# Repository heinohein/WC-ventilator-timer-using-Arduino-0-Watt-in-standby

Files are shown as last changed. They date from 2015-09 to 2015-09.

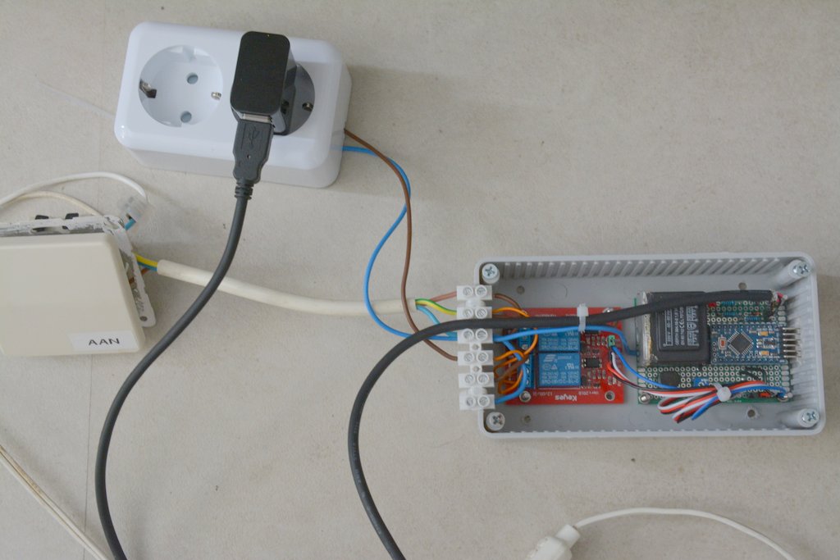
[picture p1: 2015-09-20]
WC-timer-pictures/WC timer 09 built together overview.JPG

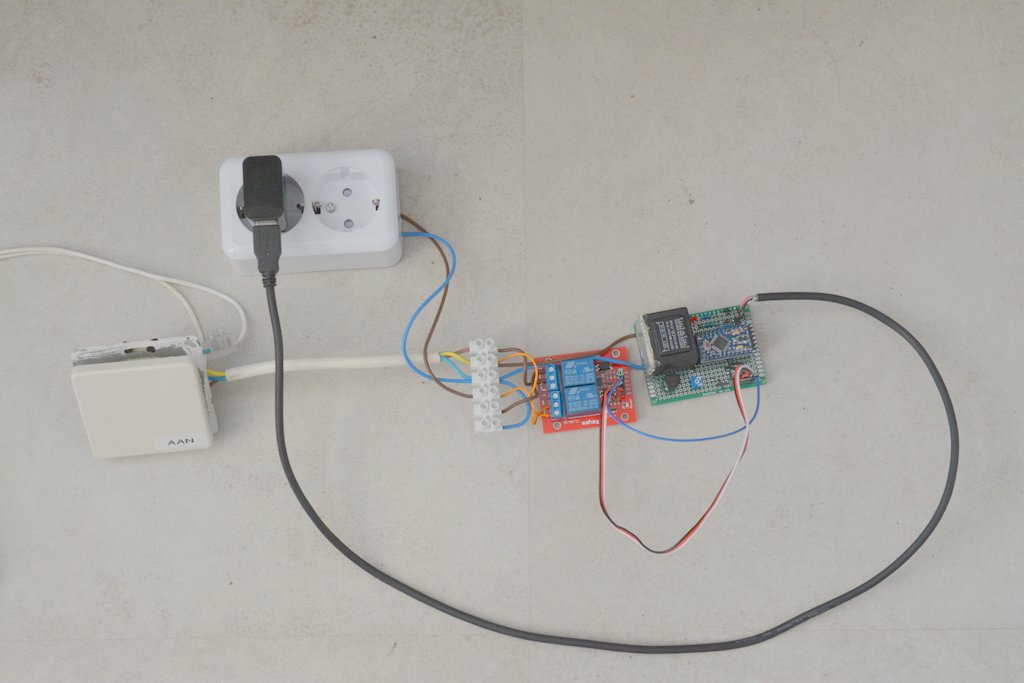
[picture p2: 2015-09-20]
WC-timer-pictures/WC timer 02 overview.JPG

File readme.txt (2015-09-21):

Timer for the motor of a WC ventilator using 0 Watt in standby

I wanted to create a timer for the ventilator in the WC, which consumes no electricity
when the timer is inactive. The project is based on using a Arduino Pro mini controling
a double relais "brick".

Priciple details:
The Arduino is fed by a 110-230V AC to 5V Dc transformer. This transformer is switched 
off AC by relais 1, hence 0 Watt standby. 
The motor of the WC ventilator is switched on/off by relais 2. 
When the lightswitch in the WC is switched on, it also provides power to Arduino. 
The Arduino detect by using a small 230V to 7,5 V transformer and some resistors 
(protected by a zener diode) that the lightswitch is switched off. This is the trigger 
that the timer can start counting down. 
The duration of the count down is variable adjustable by a potmeter.

PLEASE BE CAREFULL. 110-230V CAN KILL YOU!!.

Sketch details:
The map Arduino contains the sketch of the timer. All relevant variables are defined with
#define statements, and the sketch contains many comments for easy reading and amendment.
The sketch starts with a 10 seconds waiting. If the light in the WC is switched off during 
this time the motor of the ventilator will not run and the total electronic is switched off
again therefore using 0 Watt. If the motor of the ventilator is start running it will be 
minimal for 1 minute, independant of the input of the variable resistor. (to protect the 
motor).

Led of the Arduino:
off during initial 10 seconds wait
slow blinking during waiting for switching off 220V input (eg light WC)
faster blinking during count down and running of WC motor
very fast blinking after count down. This status is only visible if the 5V DC is not switched
off eg not the 0 Watt construction used.

PCB details:
The map Fritzing-schem-and-PCB contains a fritzing file. Inside this file you will find a
electric schem and the layout of a PCB. The schem and the PCB are also available as JPG 
in the map Wc-timer-pictures.

I designed a PCB based on a perfboard with copper solder rings on the bottom side. 
Only normal sized, not SMD components were used. 
I used for the actual build a two sided 5 x 7 cm perfboard, but did not use the toplayer 
solder rings. The few crossing wires on the topside are made of normal wires, as visible 
on the photo 05 and 06.

I could not find a propper footprint for the 230V to 7,5V AC transformer. So I used in the
schem a small audio transformer, and on the PCB I used via's to connect to the pins of the
actual transformer. This transformer feeds a led, so it is visible on the PCB that the light in
the WC is switched on.

The 230V to 5V DC transformer is switched on to power by plugging it in into a separate outlet.
Be aware that this outlet will only supply power when the WC light is switched on and the sketch
is running. See picture 02. 

The Arduino is connected to the PCB using 2x 12 pins female connector, eg the Arduino is removable.

Pictures:
Photo's of the final test setup before final installation can be found in map 
Wc-timer-pictures. 

Costs:
Total cost of the project ca. 20,45 eur/$. For details see file WC timer-bom2.html

Have fun.
HEINOHEIN

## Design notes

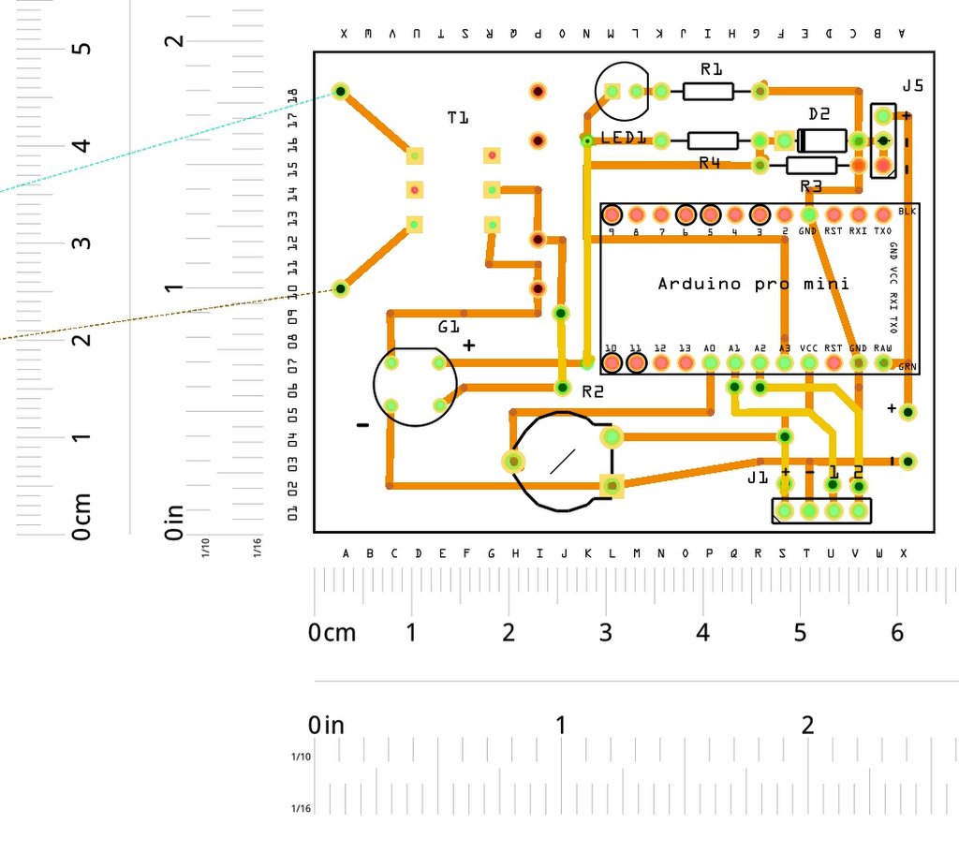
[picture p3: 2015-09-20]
WC-timer-pictures/WC timer_pcb overview.JPG

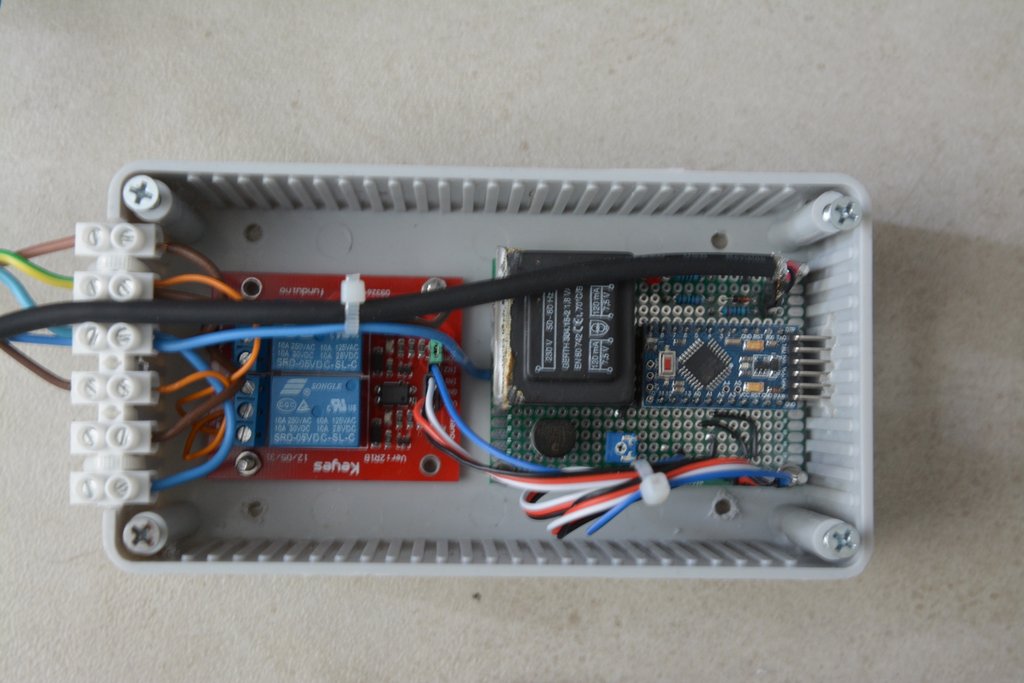
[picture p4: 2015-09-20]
WC-timer-pictures/WC timer 10 built together detail.JPG

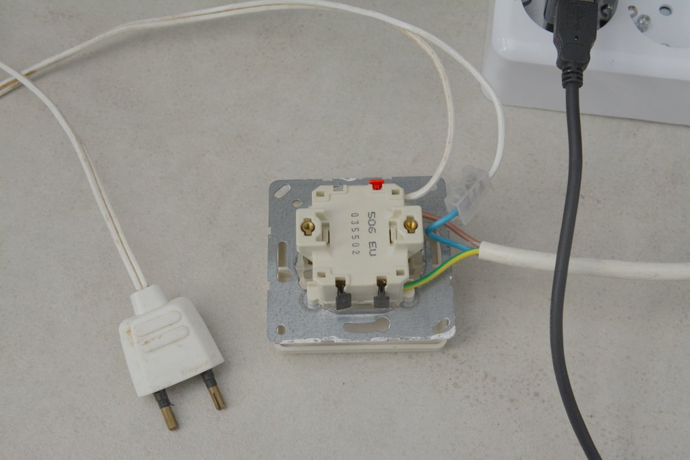
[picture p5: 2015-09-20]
WC-timer-pictures/WC timer 03 switch.JPG

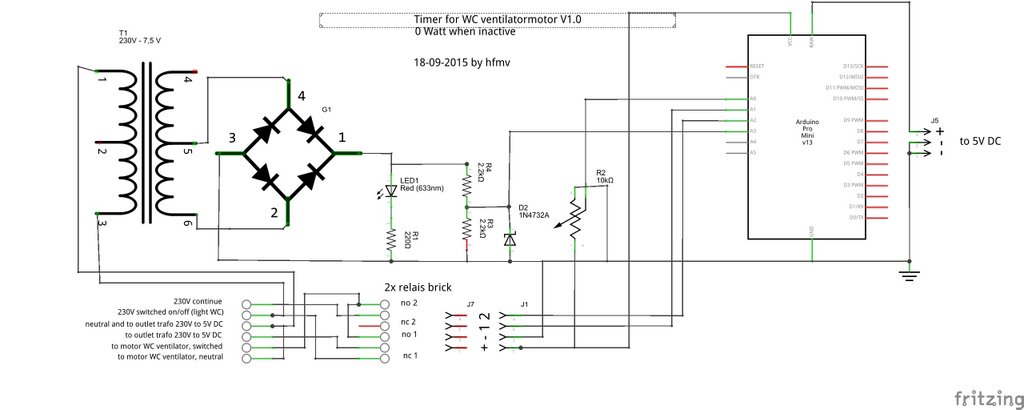
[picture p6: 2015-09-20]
WC-timer-pictures/WC timer 01 schem.JPG

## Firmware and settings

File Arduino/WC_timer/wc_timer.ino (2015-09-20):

/*
WC timer switches on and off the motor of the ventilator in a controlled way. 
Because the powersource of the Arduino (230V to 5V DC transformer) is switched on 
by the lightswitch in the WC, this system is using 0 Watt when standby.

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
written by hfmv V1.0 18-9-2015
*/
#define VERSION "V1.0"

#define LED_PIN 13                  // internal led

// input from transmiter
#define INPUT_PIN A0                // potmeter for setting variable time
#define INPUT_PIN_TXT "A0"
#define RELAIS_PIN1 A1
#define RELAIS_PIN2 A2
#define PIN_230V A3

#define ON HIGH                     // some relais have low level trigger input, in that case reverse the values
#define OFF LOW

#define START_DELAY 10000           // delay 10 seconds before doing anything

unsigned long DELAY_LED=2000;       // delay for blinking led in milli seconds
#define BLINK_FASTER_FACTOR 4       // at program end blink led x times faster

#define DELAY_RELAIS_PIN 60000      // 60 seconds = minimum time the motor is switched on 

bool start_delay = true;
unsigned long time;
unsigned long timeout;
unsigned long timeoutrelais;
bool swrelais=false;
bool swtest=true;                   

int status_led;                     // used for blinking the led
unsigned long timeled;

int timer_input;                    // input from the potentiometer
unsigned long time_factor=420;      // multiplyer to get the time in seconds from the potentiometer
//unsigned long time_factor=50;       // for tests
int i;

// ************************************************************************
void setup() {
  // Open serial communications and wait for port to open:
  Serial.begin(9600);
  while (!Serial) {
    ; // wait for serial port to connect. Needed for Leonardo only
  };
  pinMode(LED_PIN, OUTPUT);
  pinMode (INPUT_PIN, INPUT);
  pinMode(RELAIS_PIN1, OUTPUT);
  pinMode(RELAIS_PIN2, OUTPUT);
  pinMode (PIN_230V, INPUT);

  Serial.print("Start WC timer ");
  Serial.print(VERSION);
  Serial.print(", delay set by pin ");
  Serial.println (INPUT_PIN_TXT);

  time = millis();                  // get the current time
  
  digitalWrite(LED_PIN, LOW);       // initially turn the led off
  timeled=time;                     // used for blinking led
  status_led = 0;
  
  digitalWrite(RELAIS_PIN1, OFF); // turn 2x RELAIS off
  digitalWrite(RELAIS_PIN2, OFF);

  // read value external variable resistor (potentiometer)
  timer_input=analogRead(INPUT_PIN);
  if (swtest){
    Serial.print("timer_input ");
    Serial.print (timer_input);
    Serial.print (" = ");
    Serial.print (timer_input*time_factor/1000);
    Serial.println(" seconds");
  } 
  
  delay(START_DELAY);                // first wait 10 seconds before action. if power switched off in between, no motor has been running

  digitalWrite(RELAIS_PIN2, ON);   // first relais 2 to giver power back to relais 1 and to switch on motor
  delay(200);                        // give relais 2 time to settle
  digitalWrite(RELAIS_PIN1, ON);   // 220->5VDC now via relais 2 
  swrelais=true;
  
  if (swtest){
    Serial.println("wait till 230V off ");
  }

  // read input pin check if 230V "input" is still switched on
  bool timeout_230V=false;
  int value_pin_230V=0;
  int value_pin_230V_saved=0;
  while (!(timeout_230V)){
    i=analogRead(PIN_230V);
    value_pin_230V=i;
    if (value_pin_230V<100){            // suppress noise 
      value_pin_230V=0;
    }

    if (value_pin_230V==0){
      if (value_pin_230V_saved==0){
        time = millis();
        Serial.print ("waiting start at ");
        Serial.print (millis());
        Serial.print (" at ");
        Serial.println (i);
        value_pin_230V_saved=1;           // i found a 0 Volt value
      } else {
        if (millis()-time>2000){
          timeout_230V=true;             //stop waiting after 2 second 0 Volt
          Serial.print ("waiting stopped at ");
          Serial.println (millis());
        }
      }
    } else {
      value_pin_230V_saved=0;          // no continues 0 Volt found, start search again
    }
  }

   if (swtest){
    Serial.println("230V is off ");
  }
  DELAY_LED=DELAY_LED/BLINK_FASTER_FACTOR;  // change speed blinking led
  time = millis();                  // get the current time
  
} // END SETUP

void loop() {

  if (swrelais) {  
    timeout=time+timer_input*time_factor;
    timeoutrelais=time+DELAY_RELAIS_PIN;

    if (swtest) {
      Serial.print("now ");
      Serial.print(millis());
      Serial.print(" timeout ");
      Serial.print(timeout);
      Serial.print(" timeoutrelais ");
      Serial.print(timeoutrelais);
      Serial.print(" time ");
      Serial.println(time);
    }
  
    if (millis()>(timeout)){        //timed out
        if (millis()>(timeoutrelais)){ //switch relais after a minimum time
          if (swrelais) {
            Serial.println("Relais OFF");
            delay(200);             // wait finishing serial print
            DELAY_LED=DELAY_LED/BLINK_FASTER_FACTOR;  // change speed blinking led
          }
          digitalWrite(RELAIS_PIN1, OFF); // turn 2x RELAIS off
          digitalWrite(RELAIS_PIN2, OFF);
          swrelais=false;
        }
    }
  }
  if (status_led == 1){             // make LED blink
    if (millis()>(timeled+DELAY_LED)){
      digitalWrite(LED_PIN, LOW);   // turn the LED off
      status_led=0;
      timeled=millis();
    }
  } else {
    if (millis()>(timeled+DELAY_LED)){
      digitalWrite(LED_PIN, HIGH);  // turn the LED on 
      status_led=1;
      timeled=millis();
    }
  }
} // END LOOP

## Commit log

2015-09-20 Version 1.0 initial upload
    [WC timer V1.0.fzz]
2015-09-21 Added BOM
2015-09-21 BOM not visible in GitHub moved ti Fritzing map
2015-09-21 readme more details, BOM with costs added

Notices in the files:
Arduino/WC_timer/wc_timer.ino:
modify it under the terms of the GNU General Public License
